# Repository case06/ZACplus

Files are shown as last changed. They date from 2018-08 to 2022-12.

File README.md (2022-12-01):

# ZACplus

[](
    https://opensourceecology.de)

This is the source repo for the ZAC+-Projekt on

https://wiki.opensourceecology.de/Zn/O-Brennstoffzelle

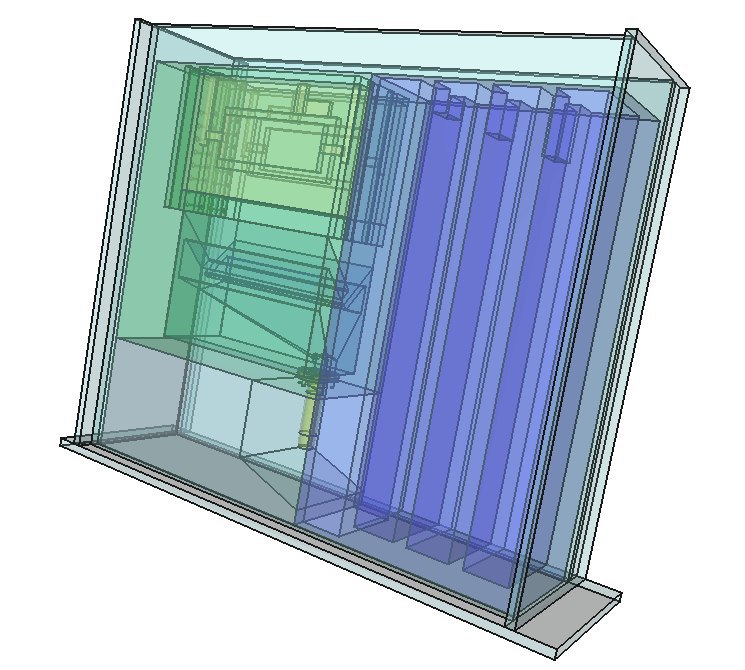
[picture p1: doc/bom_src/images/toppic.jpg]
ZACplus V.1.0
<p>  </p>

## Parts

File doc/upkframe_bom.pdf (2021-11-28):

Seite 1

UPKframe BOM

Partname | UPK-PartNo. | Quantity Description | Supplier

UPKframe
angle2 | 17092223 | 4 | Klemmung f. Tank | ML
angle4 | 17092224 | 2 | Befestigung Mittelquere | ML
angle6 | 17092225 | 8 | Eckverbindung | ML
| | | | ML
flat16 | 17092239 | 3 | f. Interface-mount u. Tank-Kammer-Verbinder | ML
flat24 | 17092240 | 3 | Bodenplatten | ML
| | | | ML
tslot16 | 17092205 | 5 | Mittelquere Front u. Aufrechte | ML
tslot24 | 17092206 | 8 | Rahmen längs u. Aufrechte | ML
tslot40 | 17092208 | 8 | Rahmen längs u. Aufrechte | ML
tslot4con | 17092212 | 2 | Aufdoppelung f. Mittelquere | ML
Tslot16con | 17092216 | 2 | Quere | ML
tslot24con | 17092217 | 8 | Rahmen, quer | ML
| | | | ML
endcap1d | 17092315 | 20 | Endkappen | ML
raconnector | 17092313 | 16 | Eckverbinder | ML
| | | | ML
m6x8 | 17092303 | 64 | Befestigung, 8mm M6, ISO 7380 | ML
m6x12 | 17092304 | 32 | Befestigung, 12mm M6, ISO 7380 | ML
m6x25cyl | 17092307 | 22 | Eckverbindungen, 25mm M6, DIN 7984 | ML
m6nutplate | 17092309 | 64 | Befestigung | ML
m6nut | 17092308 | 4 | Befestigung Interface, M6 DIN 934 | ML
m3x30cyl | 21032809 | 2 | Befestigung Pumpe, 30mm M3, DIN 7984 | ML
m3nut | 19081701 | 6 | Befestigung Pumpe, M§ DIN 934 | ML

Tank
Pumpenplatte_200x160x6 | - | 1 | Montageplatte f. Pumpe, 200x160x6 | 3DP

Seite 2

Supplier | Id | URL
Std.-Part | SP | Standard-Part, widely available from several sources
Makers-Lab ML | http:makers-lab.de
3d-Printable 3DP | 3d-printable part, see project sources
Pumpe | S1 | https://www.ebay.de/itm/351752818084?hash=item51e61a0da4:g:-pYAAOSwEK9TxksN

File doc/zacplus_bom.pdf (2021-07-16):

Seite 1

ZACplus BOM

Partname | PartNo. | Quantity Description | Supplier

Gaskathode
pone7 | 2 | Gaskathodenhalter f. GDL, 3d-part | 3DP
gdlpatch1 | 2 | Gaskathode, Gaskatel MOC | S1
m2kleber | 1 | M2 Neopren Kleber | SP, S2

Zinkanode
oberteil | 1 | Oberteil mit Schlitz f. Zinkplatte | 3DP
seitenteil1b | 2 | zum verbinden mit Oberteil | 3DP
stabilisator1b | 2 | verbindet die Seitenteile unten | 3DP
netz | 1 | muss passend gebogen werden (ev. unter Erwärmung) | 3DP
zinkplatte | 1 | zB. 0,5mm dick, 60x200mm | SP, S3

Cuvette
cuvette_bottom | 1 | Plexiglas 6mm, 412 x 116,4 mm | SP, S4
cuvette_side | 2 | Plexiglas 6mm, 360 x 320 mm | SP, S4
cuvette_frontback | 2 | Plexiglas 6mm, 320 x 116,4 mm | SP, S4
UHUhart | 1 | Kleber f. Plexiglas | SP, S5
silikon | 1 | Eckenfugen ausschmieren | SP, S6

Reaktionskammer
kammer_01 | 1 | Reaktionskammer | 3DP
devolume1 | 1 | Devoluminator | 3DP
emscherbrunnen_01 | 1 | Rutsche/Führung f. Zinc-Slurry | 3DP
schlauchtuelle_03 | 1 | Auslass | 3DP
kaskade1 | 1 | Absetz-Mehrkammersystem | 3DP

Seite 2

Supplier | Id | URL
Std.-Part | SP | Standard-Part, widely available from several sources
Makers-Lab ML | http:makers-lab.de
3d-Printable 3DP | 3d-printable part, see project sources
Gaskatel | S1 | https://gaskatel.de/en/shop/moc-airelectrode-without-ptfe-gasdiffusionlayer/
ebay | S2 | https://www.ebay.de/itm/372711968571?hash=item56c75d4f3b:g:nwYAAOSww6NdKfrM
ebay | S3 | https://www.ebay.de/itm/381164961784?hash=item58bf33bff8:g:qKkAAOSwLs9aYJlP
ebay | S4 | https://www.ebay.de/itm/264805134763?hash=item3da79db1ab:g:sY0AAOSwo8FfGGdu
ebay | S5 | https://www.ebay.de/itm/282102926692?epid=2255354665&hash=item41aea50d64:g:PJwAAOSwiO9Xie7J
ebay | S6 | https://www.ebay.de/itm/124598821921?hash=item1d02ab2421:g:se4AAOSwK-Fgh59I

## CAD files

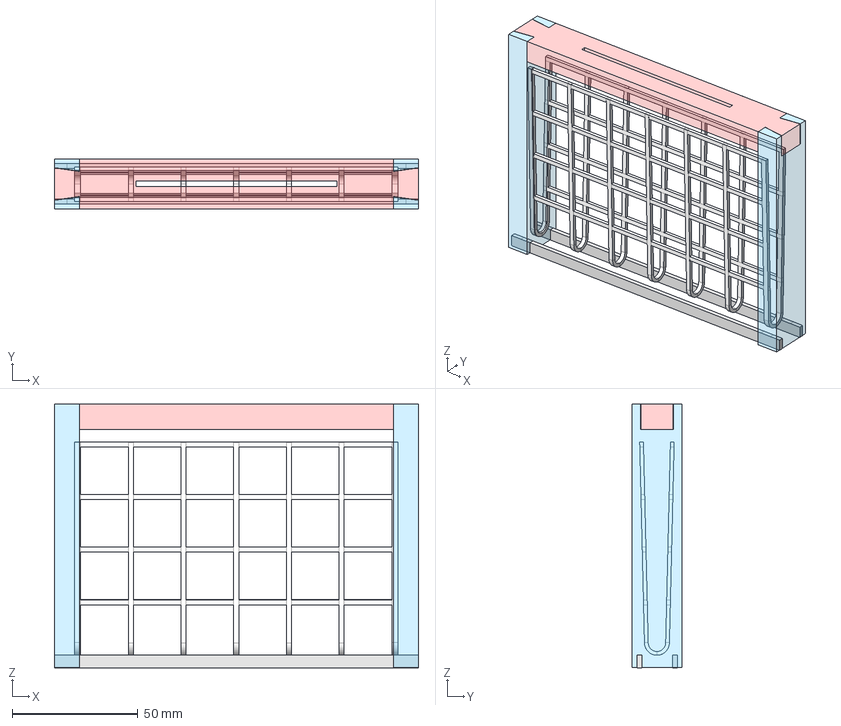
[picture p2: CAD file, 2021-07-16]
cadfiles/zinkanode/Assembly-Zinkplattenhalter.fcstd
145.0 x 19.8 x 105.0 mm
Seitenteil01
Seitenteil01 (Mirror #2)

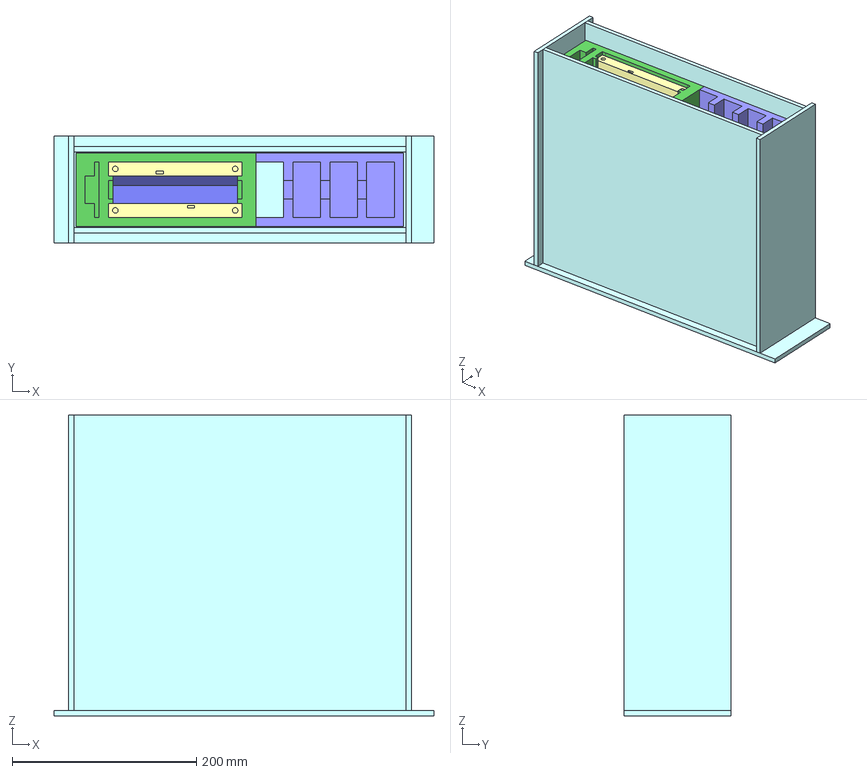
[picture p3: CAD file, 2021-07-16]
cadfiles/kammer/assembly2c.fcstd
412.0 x 116.4 x 326.0 mm
chamber
cascade
devolume
pipe
emscherbrunnen
gdlholder
gdlholder001
cuvette_bottom
cuvette_side
cuvette_side001
cuvette_front
cuvette_front001

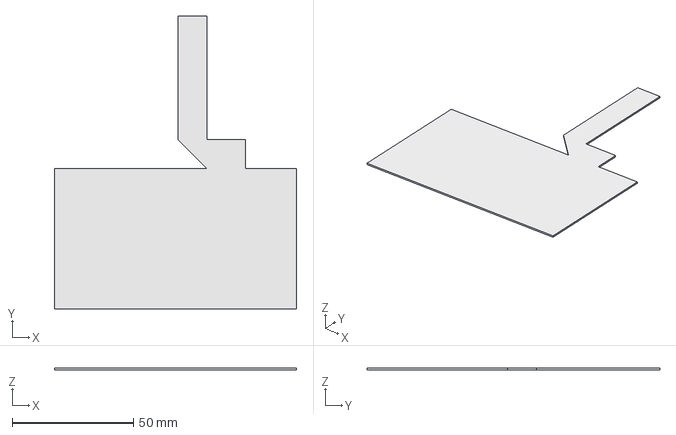
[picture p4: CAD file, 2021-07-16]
cadfiles/gaskathode/gdlpatch1.fcstd
100.0 x 121.0 x 0.7 mm

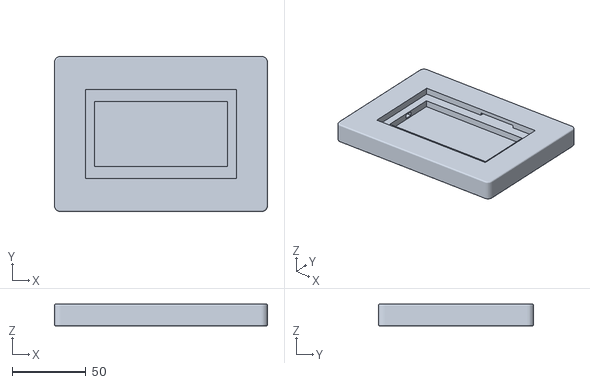
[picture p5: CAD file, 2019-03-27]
cadfiles/gaskathode/stls/pone6b_rounded.stl
144.0 x 105.0 x 14.8

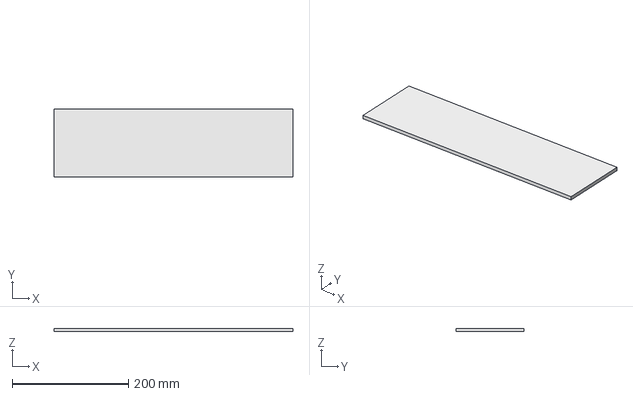
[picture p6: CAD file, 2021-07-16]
cadfiles/kammer/cuvette_bottom.fcstd
412.0 x 116.4 x 6.00 mm

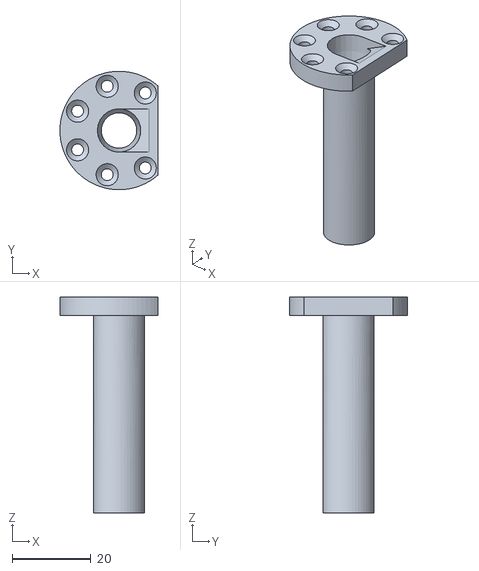
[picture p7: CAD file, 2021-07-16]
cadfiles/kammer/stls/schlauchtuelle_03b.stl
24.9 x 30.0 x 54.8

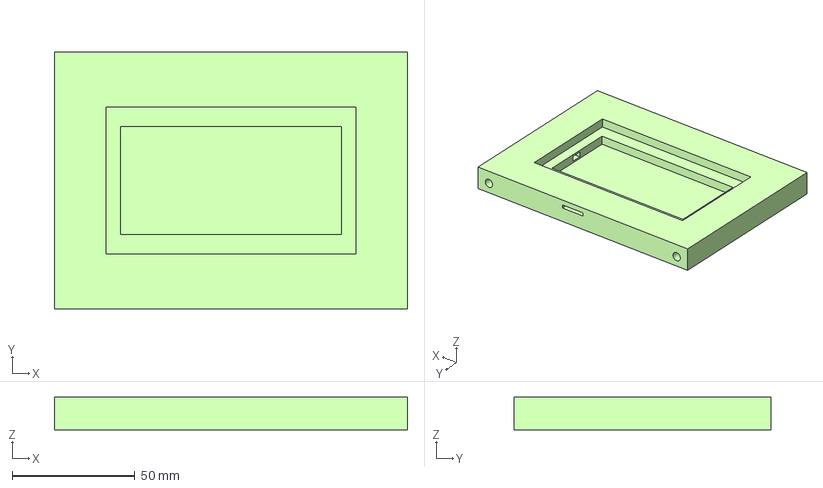
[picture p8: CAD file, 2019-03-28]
cadfiles/gaskathode/pone7.fcstd
144.0 x 105.0 x 13.4 mm

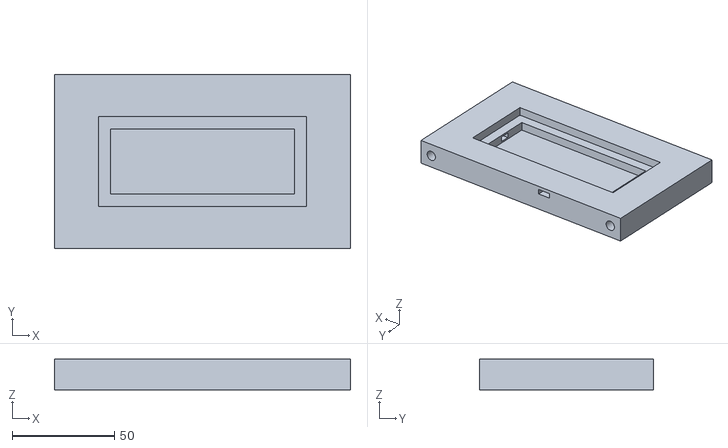
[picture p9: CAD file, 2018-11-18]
cadfiles/gaskathode/stls/pone5.stl
145.0 x 85.0 x 15.0

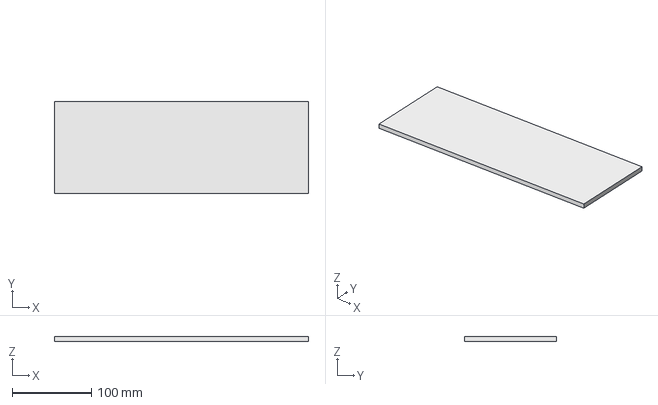
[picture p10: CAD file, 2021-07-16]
cadfiles/kammer/cuvette_frontback.fcstd
320.0 x 116.4 x 6.00 mm

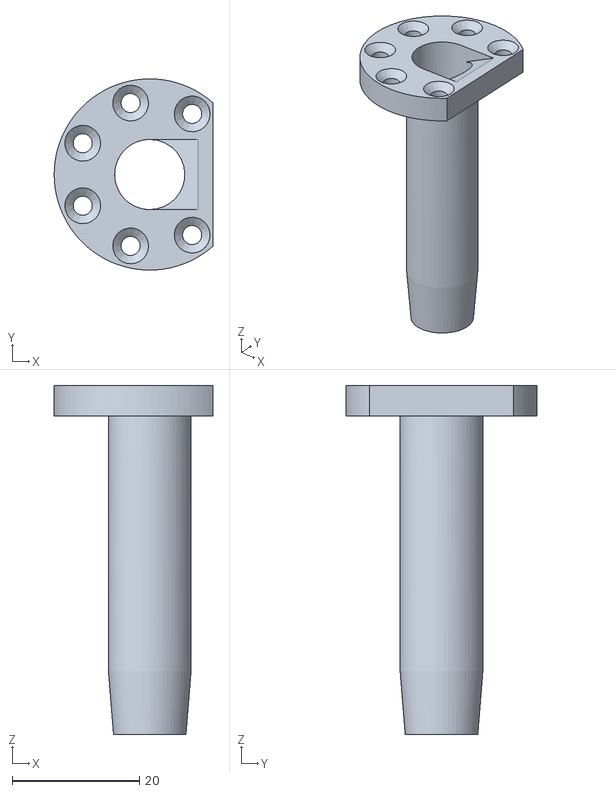
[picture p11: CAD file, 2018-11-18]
cadfiles/kammer/stls/schlauchtuelle_02.stl
24.9 x 30.0 x 54.8

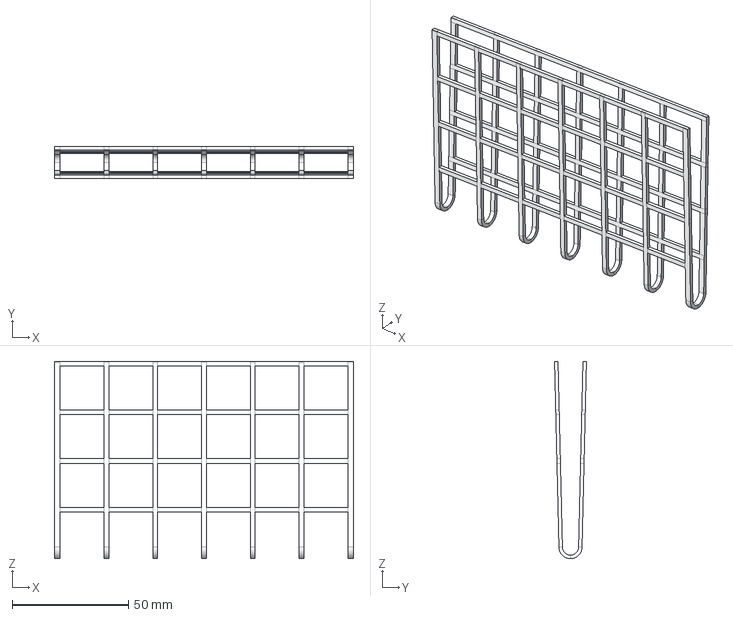
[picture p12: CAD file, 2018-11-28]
cadfiles/zinkanode/Netz_gebogen.fcstd
128.8 x 13.8 x 85.0 mm

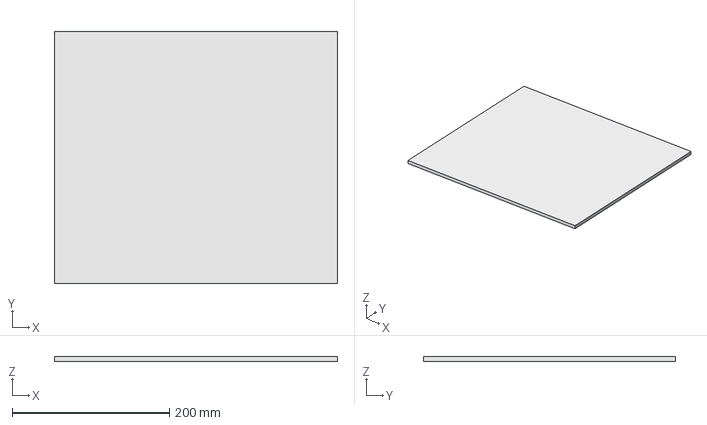
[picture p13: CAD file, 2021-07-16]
cadfiles/kammer/cuvette_side.fcstd
360.0 x 320.0 x 6.00 mm

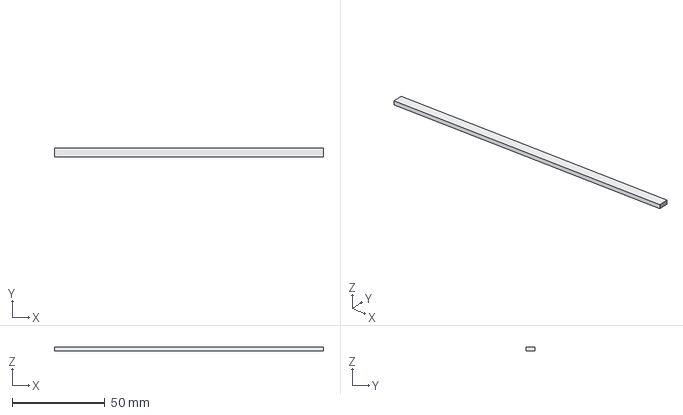
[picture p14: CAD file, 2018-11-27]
cadfiles/zinkanode/Stabilisator1b.fcstd
145.0 x 5.00 x 2.00 mm

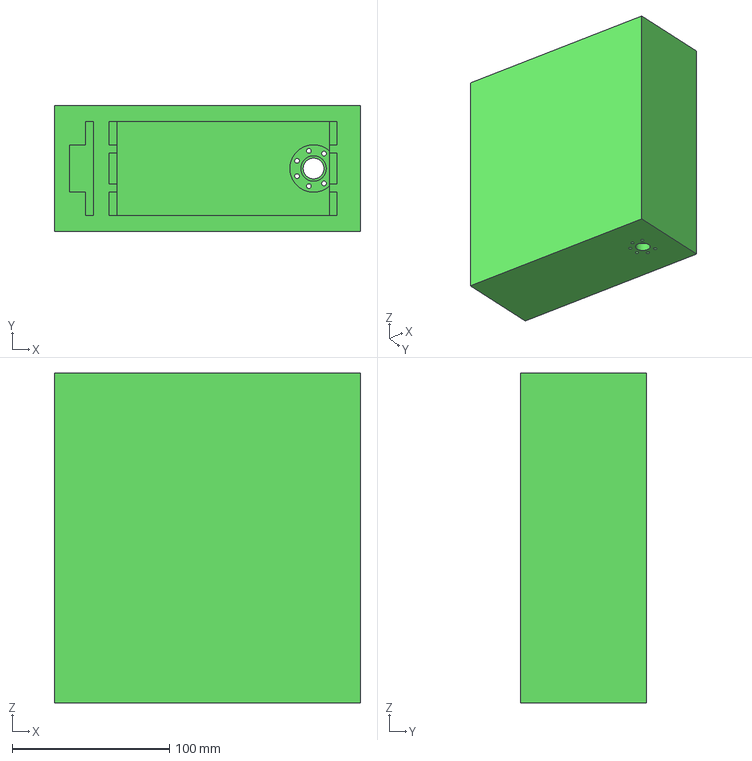
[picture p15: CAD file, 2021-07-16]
cadfiles/kammer/kammer_01.fcstd
195.0 x 80.0 x 210.0 mm

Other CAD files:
cadfiles/gaskathode/pone7_rounded.fcstd
cadfiles/zinkanode/Netz.fcstd
cadfiles/kammer/schlauchtuelle_03.fcstd
cadfiles/zinkanode/Seitenteil1b.fcstd
cadfiles/kammer/devolume1.fcstd
cadfiles/kammer/emscherbrunnen_01.fcstd
cadfiles/kammer/kammer_00.fcstd
cadfiles/kammer/kammer_01_drawdim.fcstd
cadfiles/kammer/kaskade1.fcstd
cadfiles/kammer/stls/devolume1.stl
cadfiles/kammer/stls/emscherbrunnen_01.stl
cadfiles/kammer/stls/kammer_01.stl
cadfiles/kammer/stls/kaskade1.stl
cadfiles/kammer/stls/schlauchtuelle_03.stl
cadfiles/zinkanode/Oberteil.fcstd
cadfiles/zinkanode/stls/netz.stl
cadfiles/zinkanode/stls/oberteil.stl
cadfiles/zinkanode/stls/seitenteil1b.stl
cadfiles/zinkanode/stls/stabilisator1b.stl

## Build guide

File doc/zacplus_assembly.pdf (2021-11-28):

Sheet1

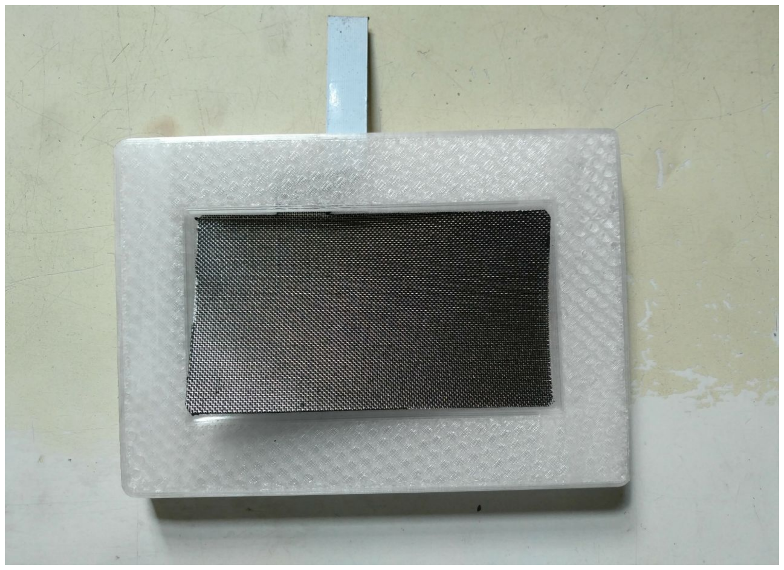
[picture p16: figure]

Page 1

ZACplus Subassemblie BOM

Die Gaskathode mit Halter

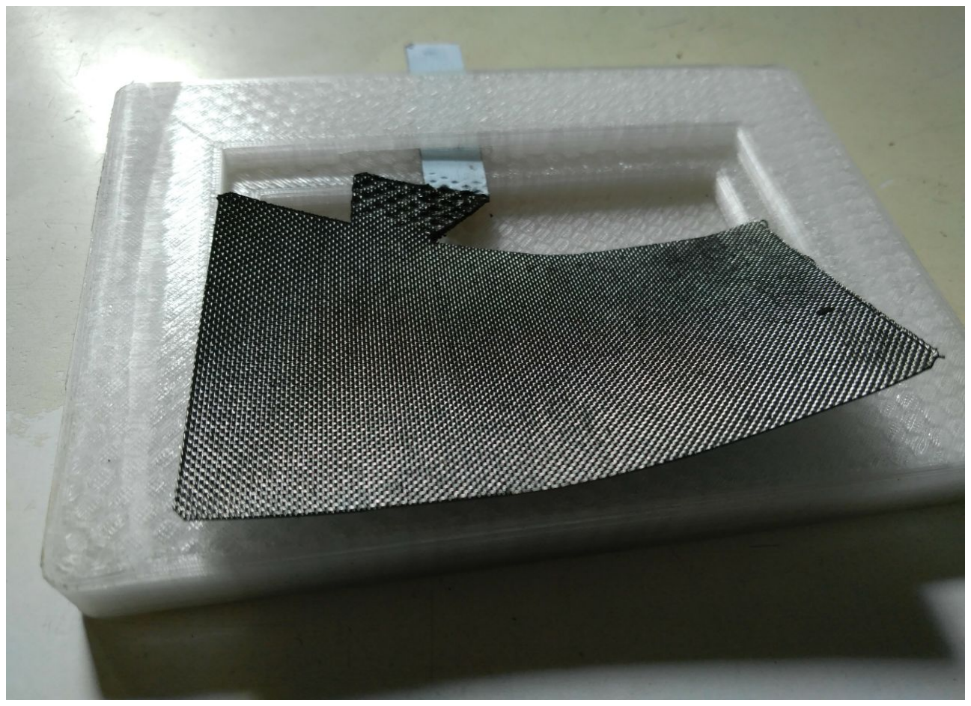
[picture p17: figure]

Sheet1

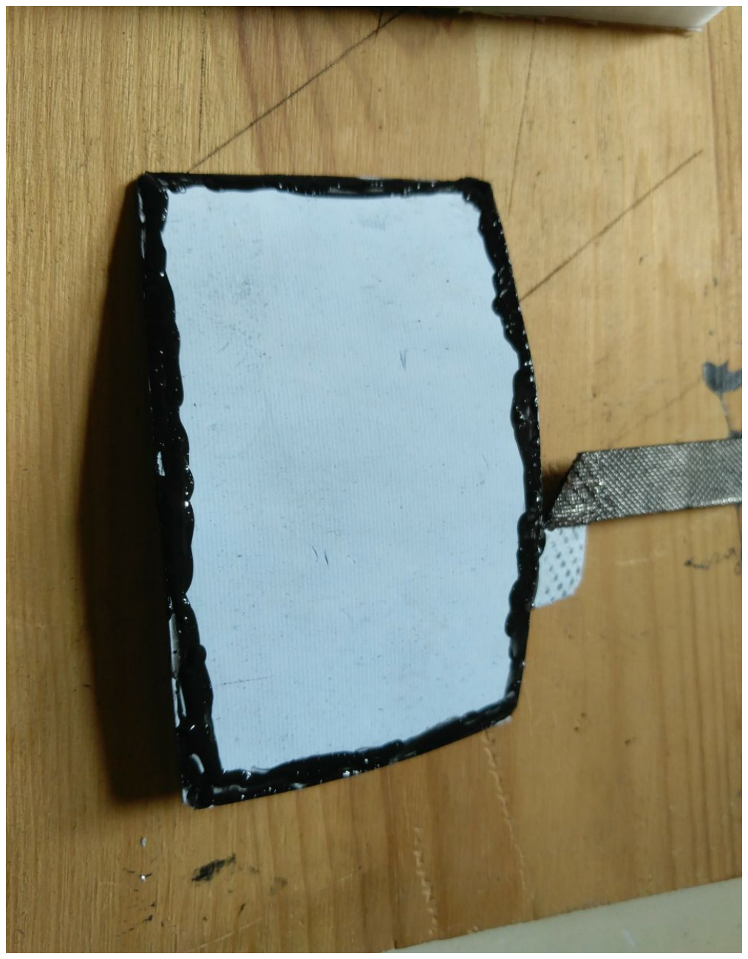
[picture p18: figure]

Page 2

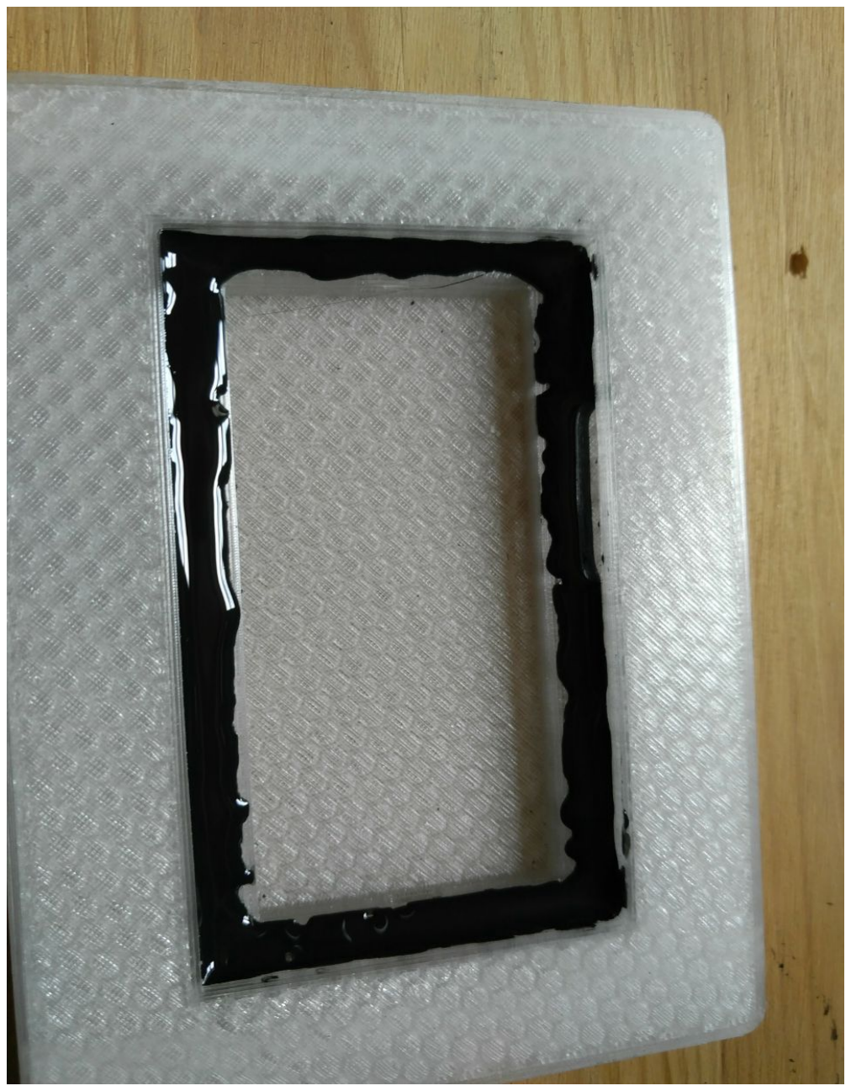
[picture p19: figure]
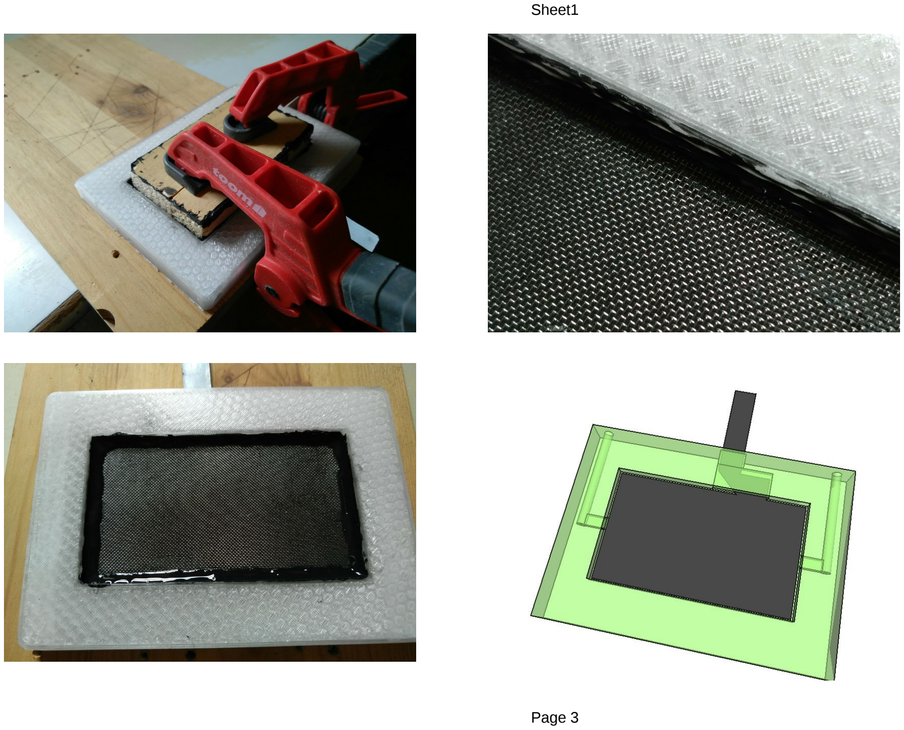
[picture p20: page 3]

Sheet1

Page 3

Sheet1

Page 4

Den GDL-patch passend ausschneiden, die Lasche um 90° drehen/rumbiegen und plattdrücken.

Den Falz vom Gaskathodenhalter mit M2 Kleber bestreichen. Den Rand der GDL auf d. PTFE-Seite ebenfalls mit M2 Kleber versehen. Dann die Lasche der GDL durch den Schlitz im Kathodenhalter fädeln und die GDL mittels Zulage einpressen.

Nun die GDL im Falz nochmal gitterseitig mit M2-Kleber füllen zwecks Abdichtung.

Gaskathode
pone7 | 2 | Gaskathodenhalter f. GDL, 3d-part
gdlpatch1 | 2 | Gaskathode, Gaskatel MOC
m2kleber | 1 | M2 Neopren Kleber

Die Zinkanode mit Halter

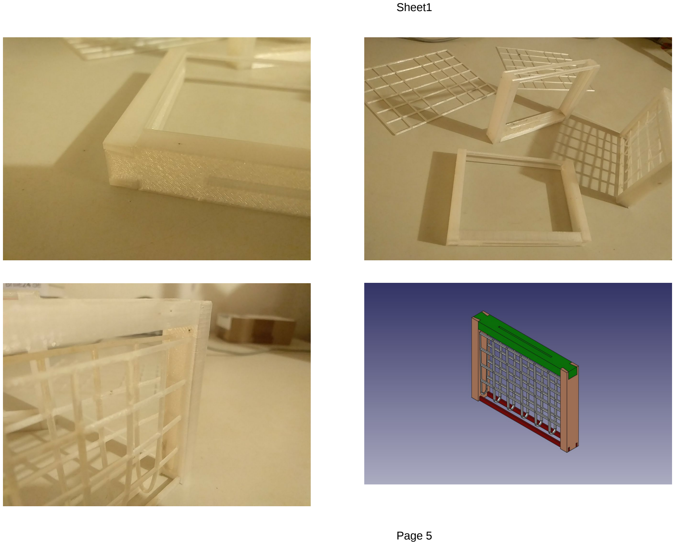
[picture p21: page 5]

Sheet1

Page 5

Sheet1

Page 6

Das Netz passend biegen, dazu den mittleren zu biegenden Bereich leich mit einer Feuerzeugflamme erwärmen.

Das Oberteil und die beiden Seitenteile durch Schwalbenschwanzverbindung verbinden / reindrücken, dazu vorher die Verbindungsstellen mit ABS-Juice (in Azenton gelöstes ABS) bestreichen.

Das gebogene Netz in die Nuten der Seitenteile mit ABS-Juice einkleben.
Die Seitenteile unten mit den STabilisatoren verbinden.

Zinkanode
oberteil | 1 | Oberteil mit Schlitz f. Zinkplatte
seitenteil1b | 2 | zum verbinden mit Oberteil
stabilisator1b | 2 | verbindet die Seitenteile unten
netz | 1 | muss passend gebogen werden (ev. unter Erwärmung)
zinkplatte | 1 | zB. 0,5mm dick, 60x200mm

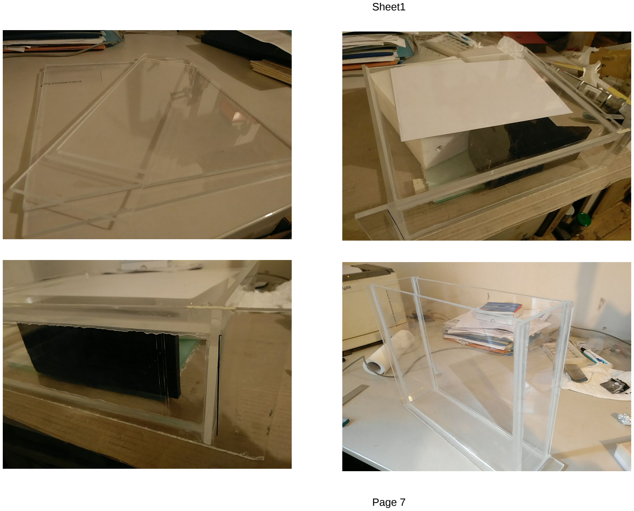
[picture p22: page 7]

Sheet1

Page 7

Die Kammer mit umgebender Cuvette

Sheet1

Page 8

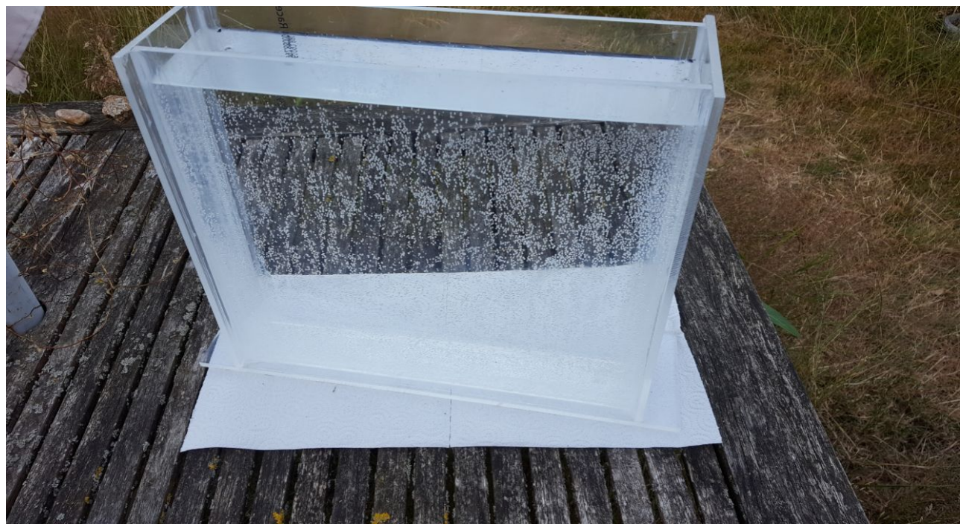
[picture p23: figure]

Den Boden der Cuvette zunächst mit den Seitenteilen verkleben und dann alles mit der einen Seite verkleben. Als Kleber wird UHUhart verwendet.
Dann das Ganze auf die Seite legen, die 3d-gedruckten Kammerteile als Abstandshalter
dazwischenlegen und die noch fehlende Seite aufkleben.
Die Kammerteile müssen leichtgängig einschiebbar sein.
Anschliessend sämtliche Eckfugen mit einer Silikon-Wulst auskleiden zwecks größerer Dichtigkeit. Dichtigkeit abschliessend testen.

Sheet1

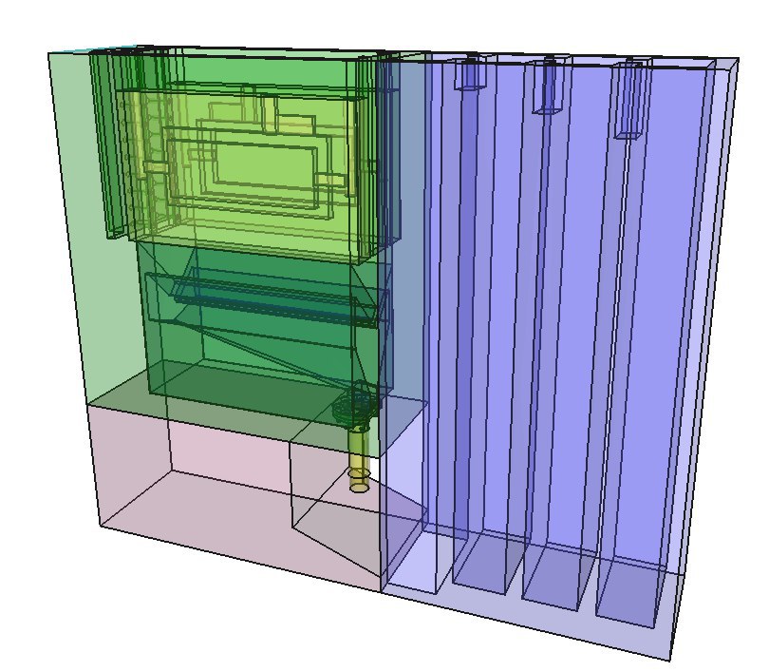
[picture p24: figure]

Page 9

Cuvette
cuvette_bottom | 1 | Plexiglas 6mm, 412 x 116,4 mm
cuvette_side | 2 | Plexiglas 6mm, 360 x 320 mm
cuvette_frontback | 2 | Plexiglas 6mm, 320 x 116,4 mm
UHUhart | 1 | Kleber f. Plexiglas
silikon | 1 | Eckenfugen ausschmieren

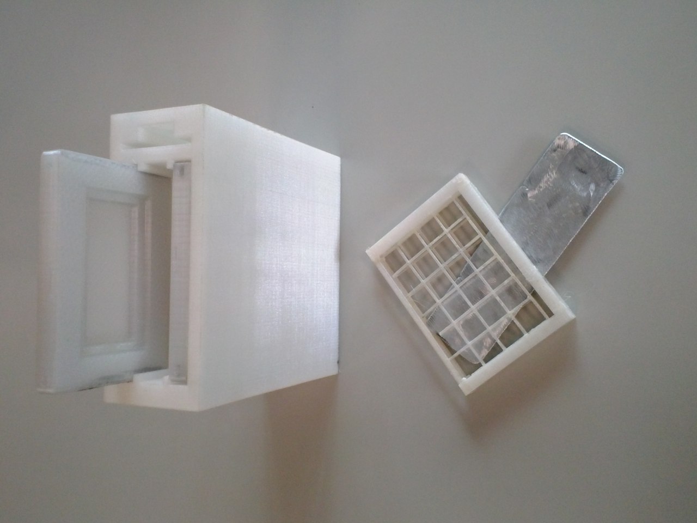
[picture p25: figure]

Sheet1

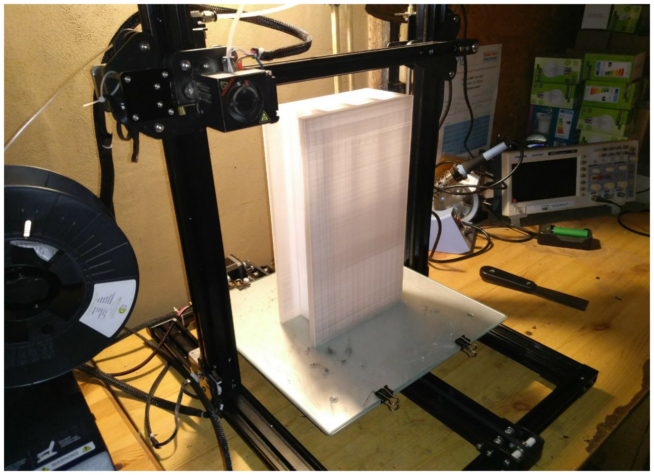
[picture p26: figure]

Page 10

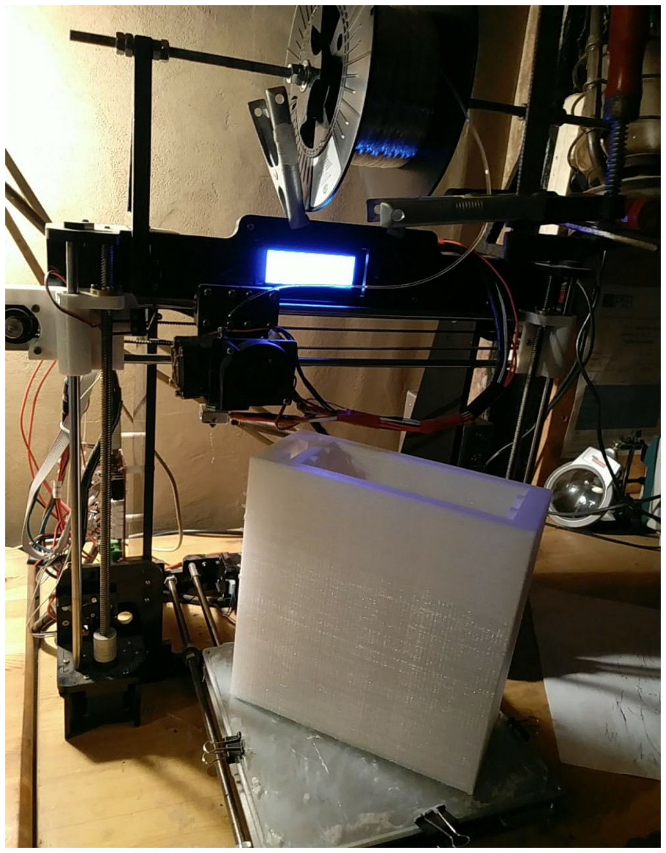
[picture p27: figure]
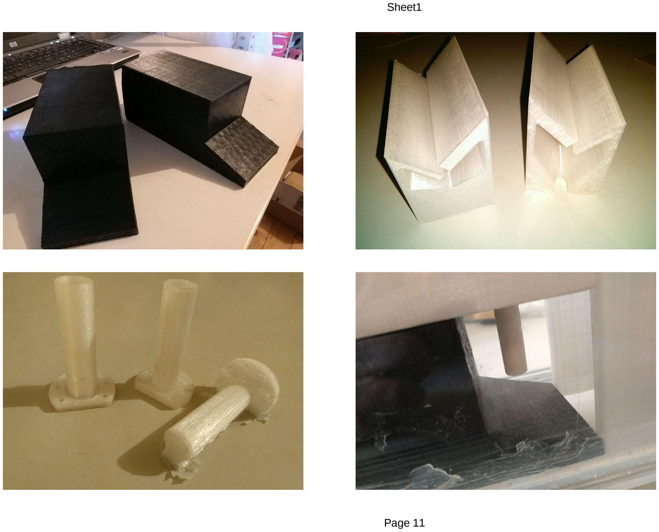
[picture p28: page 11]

Sheet1

Page 11

Sheet1

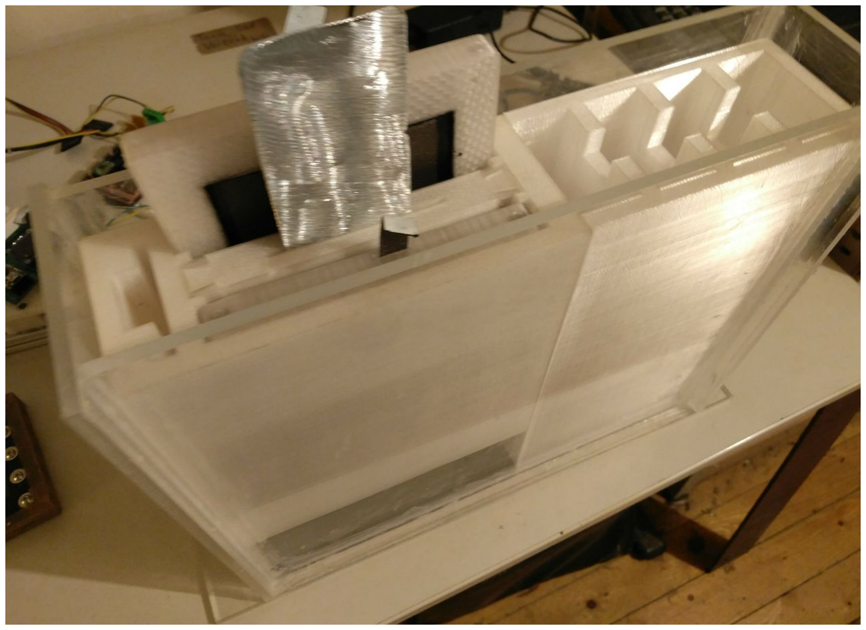
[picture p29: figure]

Page 12

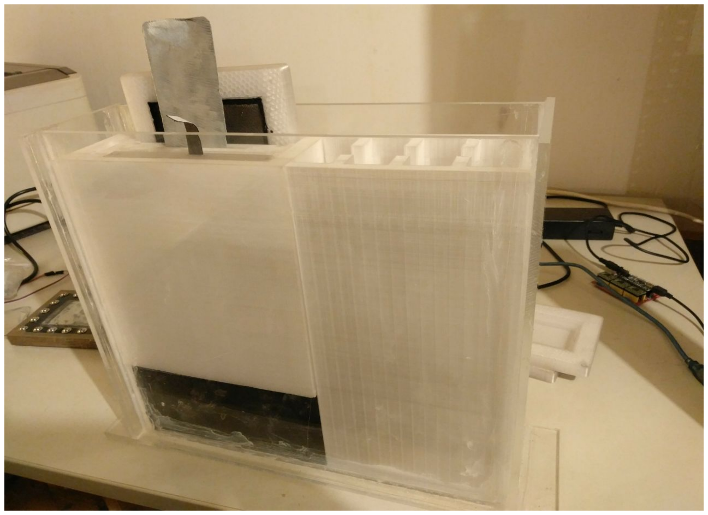
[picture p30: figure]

Die Schlauchtuelle durch die Auslassöffnung am Grunde der Kammer schieben, hält klemmschlüssig.
Dann den Emscherbrunnen in die Kammer schieben. Im oberen Bereich noch die beiden Gaskathodenhalter und den Zinkanodenhalter einschieben.

Nun den Devoluminator in die Cuvette schieben und die Kammer oben drauf setzen. Den verbleibenden Raum
daneben in der Cuvette mit der Kaskadenkammer ausfüllen, indem das Kaskaden-Modul dort eingeschoben wird.

Reaktionskammer
kammer_01 | 1 | Reaktionskammer
devolume1 | 1 | Devoluminator
emscherbrunnen_01 | 1 | Rutsche/Führung f. Zinc-Slurry
schlauchtuelle_03 | 1 | Auslass
kaskade1 | 1 | Absetz-Mehrkammersystem

Sheet1

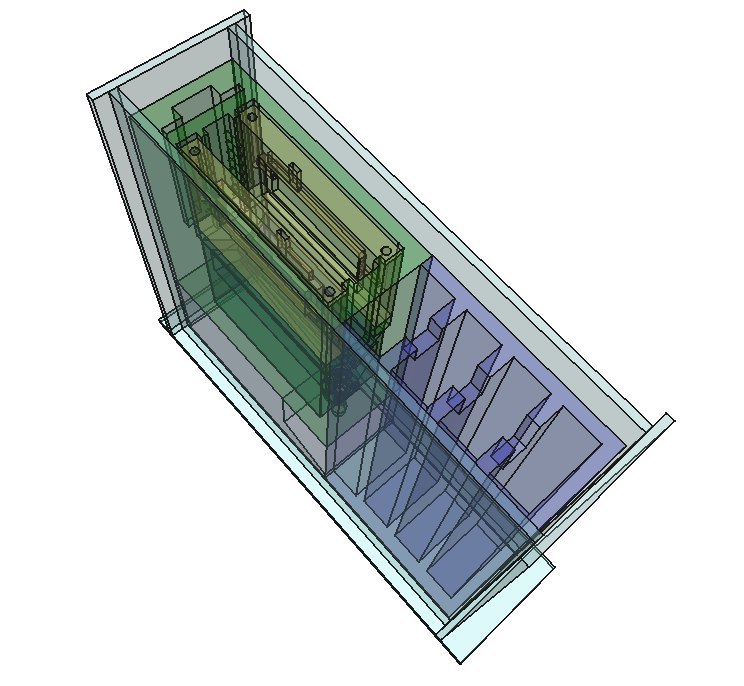
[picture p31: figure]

Page 13


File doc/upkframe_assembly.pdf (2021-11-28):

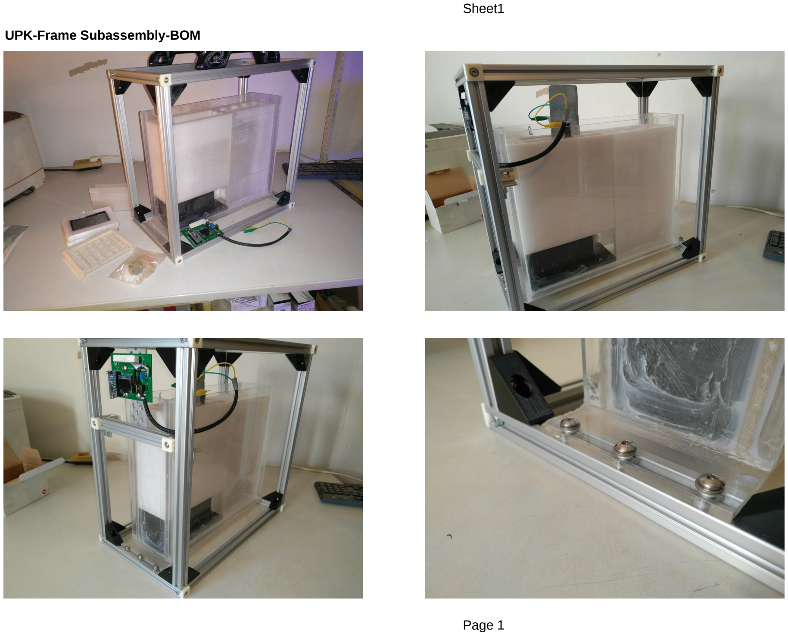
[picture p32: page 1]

Sheet1

Page 1

UPK-Frame Subassembly-BOM

Sheet1

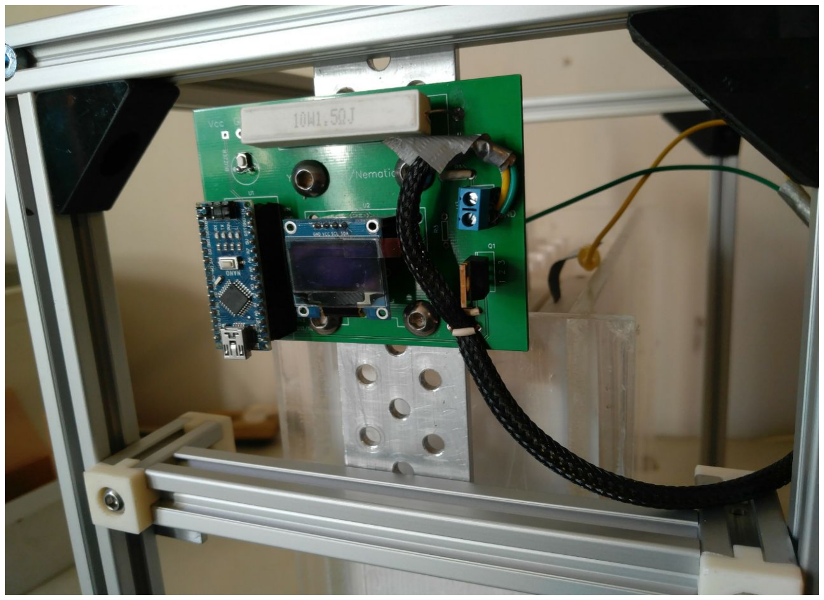
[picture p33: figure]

Page 2

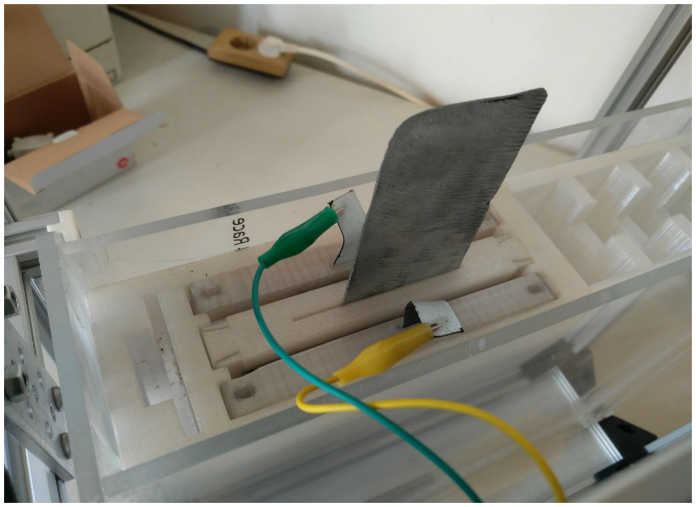
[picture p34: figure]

Unterer u. oberer Rahmen f. Kammer
tslot24con | 4 | Rahmen, quer
tslot40 | 4 | Rahmen längs
m6x25cyl | 8 | Eckverbindungen
endcap1d | 8 | Endkappen
m6x8 | 8 | Befestigung Endkappen

Sheet1

Page 3

Aufrechte f. Rahmen
tslot40 | 4 | Rahmen Aufrechte
raconnector | 16 | Eckverbinder
m6x12 | 16 | Befestigung Eckverbinder
m6nutplate | 16 | Befestigung Eckverbinder

Mittelquere
tslot16 | 1 | Mittelquere Front
tslot4con | 2 | Aufdoppelung f. Mittelquere
m6x25cyl | 2 | Eckverbindung Mittelquere
endcap1d | 4 | Endkappen
m6x8 | 4 | Befestigung Endkappen
angle4 | 2 | Befestigung Mittelquere
m6nutplate | 4 | Befestigung Mittelquere
m6x8 | 4 | Befestigung Mittelquere

Interface-Träger
flat16 | 1 | f. Interface-Montage
m6nutplate | 4 | Befestigung flat16
m6x8 | 4 | Befestigung flat16
m6x12 | 4 | Befestigung Interface
m6nut | 4 | Befestigung Interface

Verbindung Kammer-Tank
flat16 | 2 | Verbindet Tankmodul mit Kammer
m6nutplate | 8 | Befestigung flat16
m6x8 | 8 | Befestigung flat16

Sheet1

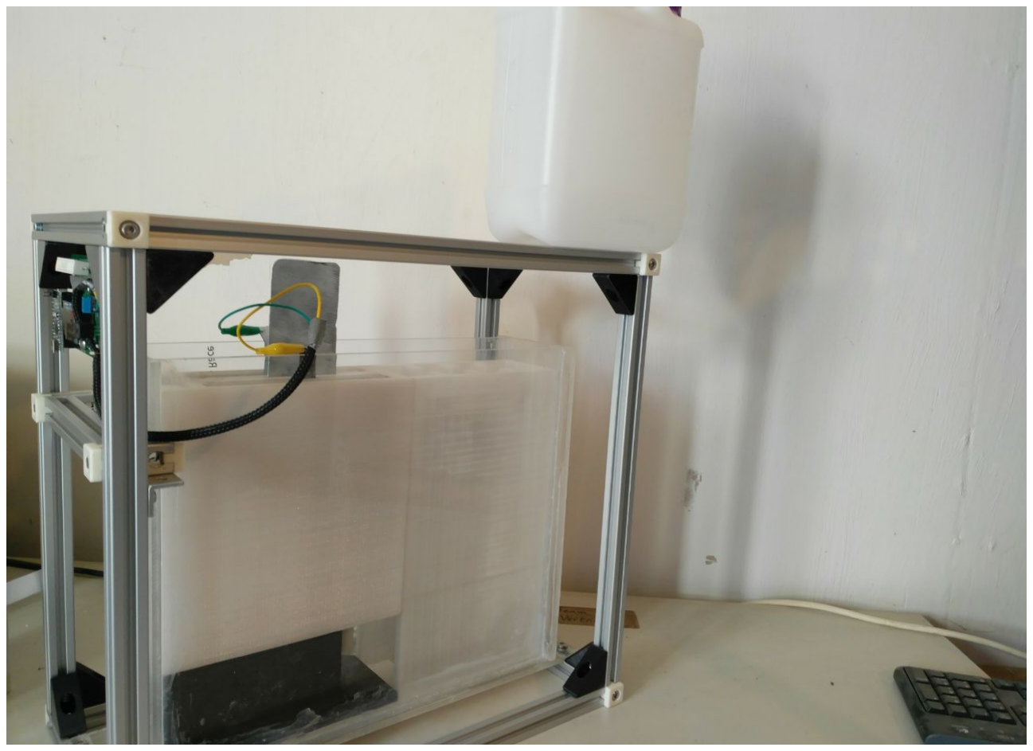
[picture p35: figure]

Page 4

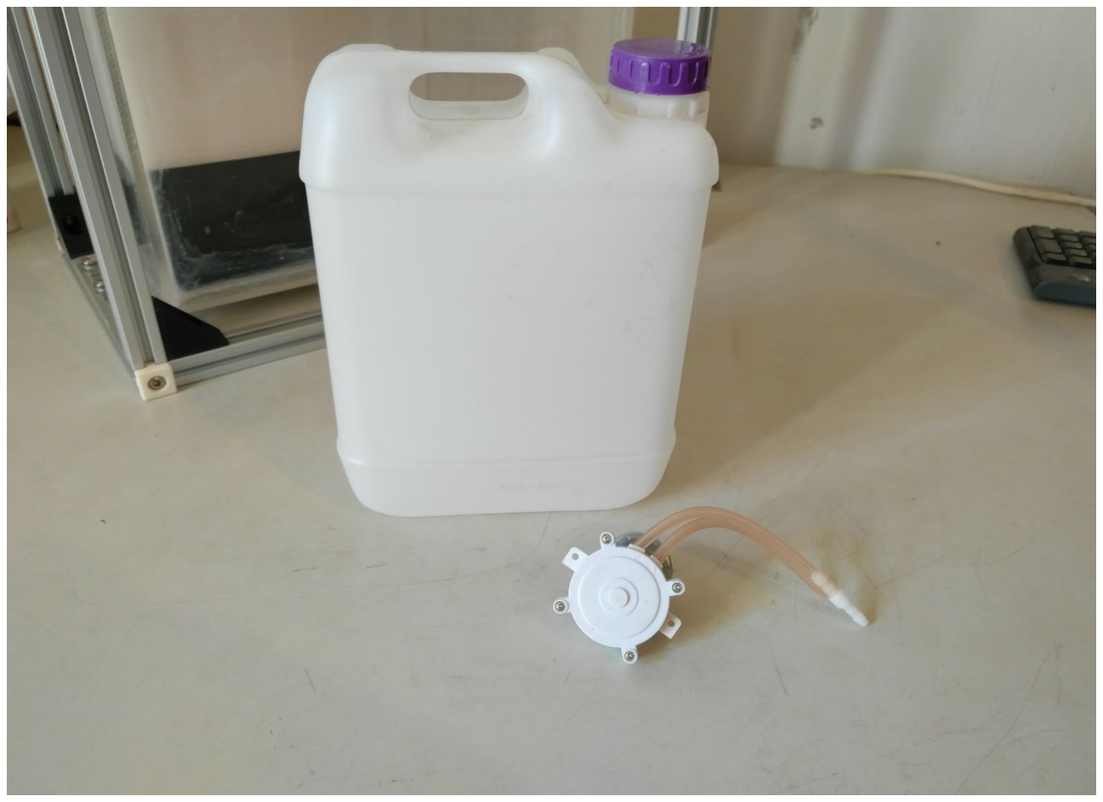
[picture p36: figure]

Sheet1

Page 5

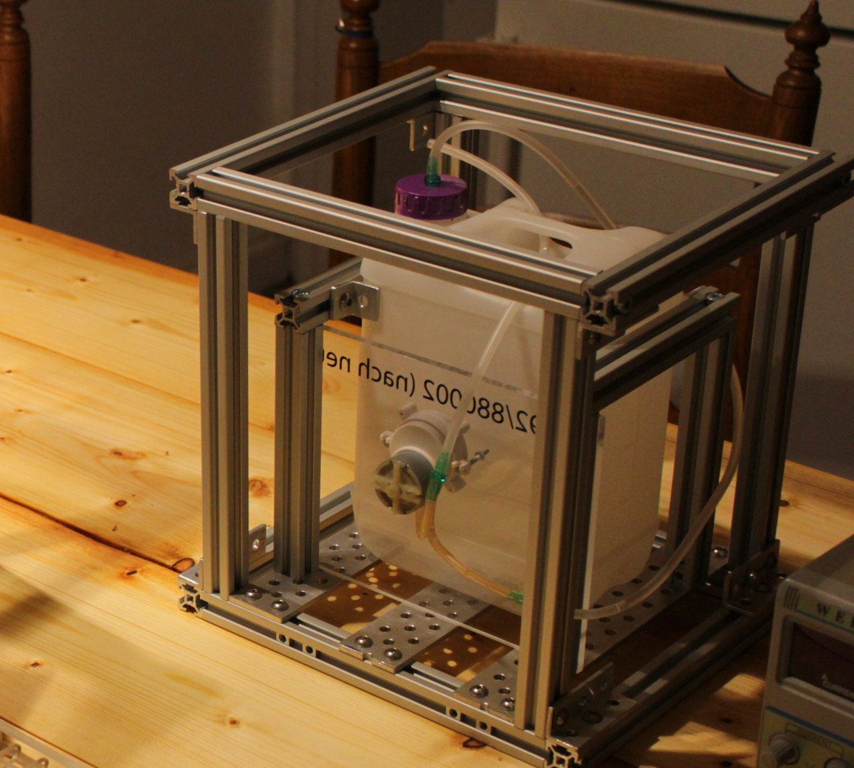
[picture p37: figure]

Unterer u. oberer Rahmen f. Tank
tslot24con | 4 | Rahmen, quer
tslot24 | 4 | Rahmen längs
m6x25cyl | 8 | Eckverbindungen
endcap1d | 8 | Endkappen
m6x8 | 8 | Befestigung Endkappen

Aufrechte f. Rahmen
tslot24 | 4 | Rahmen Aufrechte

Sheet1

Page 6

angle6 | 8 | Eckverbindung
m6nutplate | 16 | Befestigung Eckverbindung
m6x8 | 16 | Befestigung Eckverbindung
flat24 | 3 | Bodenplatten
m6nutplate | 12 | Befestigung Bodenplatten
m6x8 | 12 | Befestigung Bodenplatten

Tankhalter
Tslot16con | 2 | Quere
Tslot16 | 4 | Aufrechte
m6x25cyl | 4 | Befestigung oben
m6x12 | 4 | Befestigung unten
angle2 | 4 | Klemmung f. Tank
m6x12 | 4 | Befestigung angle2

Zirkulationspumpe
Pumpenplatte_200x160 | 1 | Montageplatte f. Pumpe
m6x12 | 4 | Befestigung d. Platte
m6nutplate | 4 | Befestigung d. Platte
circulationpump12v24l | 1 | Peristaltikpumpe, 24L/h
m3x30 | 2 | Befestigung Pumpe
m3nut | 6 | Befestigung Pumpe

Tank
Tank2.5L | 1 | 2,5L-Behälter, 220x160x100
Schlauch6mm | 2 | Silikonschlauch 6mm, 50mm
Stutzen 6mm | 3 | Anschlussstutzen f. Schlauch

Sheet1

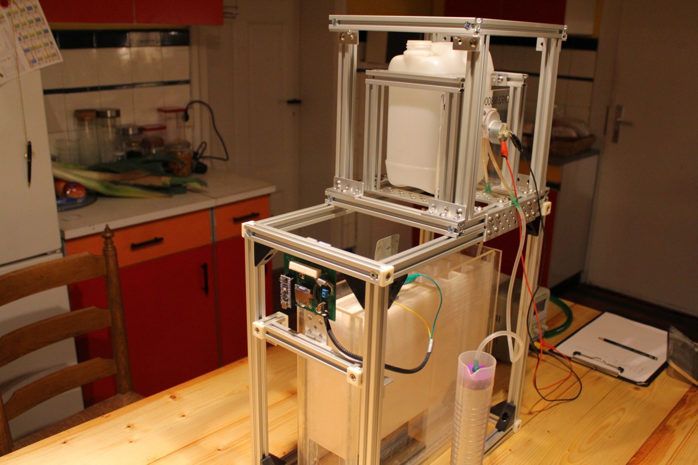
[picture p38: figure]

Page 7

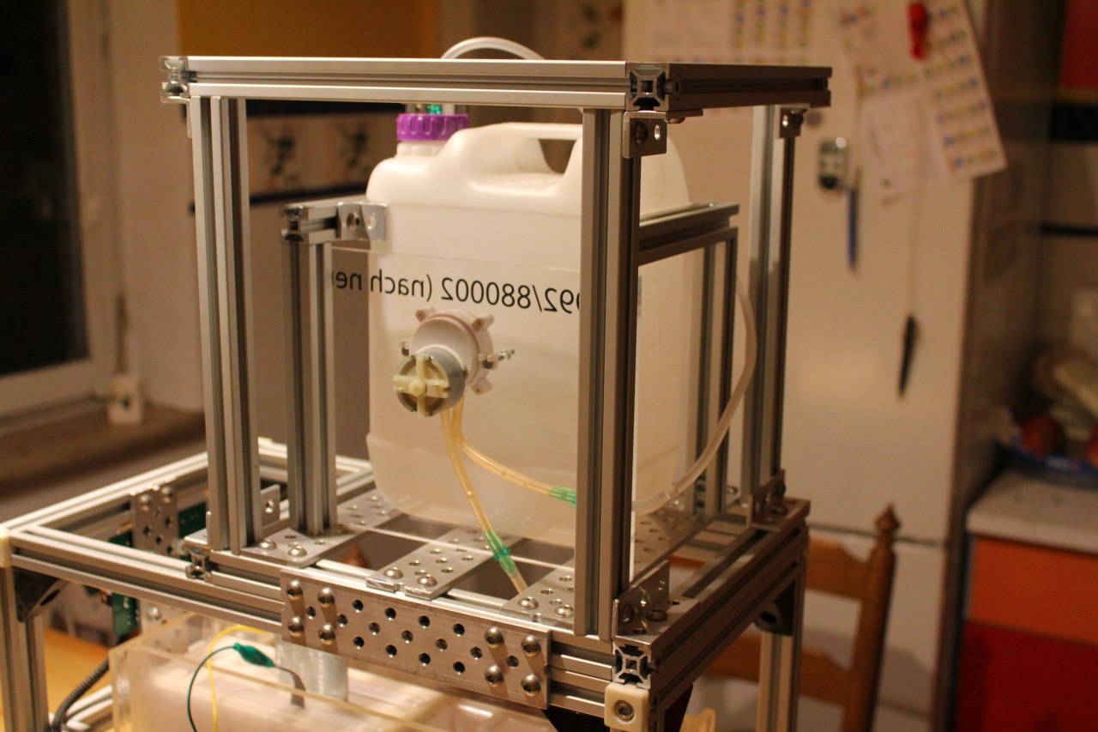
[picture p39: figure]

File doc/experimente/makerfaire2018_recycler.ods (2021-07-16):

mA | V
0 | 1,7
10 | 1,8
20 | 1,9
40 | 2
80 | 2,1
110 | 2,2
130 | 2,3
170 | 2,4
210 | 2,5
230 | 2,6
290 | 2,7
340 | 2,8
380 | 2,9
420 | 3
470 | 3,1
490 | 3,2
530 | 3,3
560 | 3,4
600 | 3,5
640 | 3,6
670 | 3,7
700 | 3,8
740 | 3,9
770 | 4
810 | 4,1
850 | 4,2
900 | 4,3
940 | 4,4
970 | 4,5
1020 | 4,6
1050 | 4,7
1080 | 4,8
1100 | 4,9
1160 | 5
1200 | 5,1
1240 | 5,2
1280 | 5,3
1300 | 5,4
1320 | 5,5
1360 | 5,6
1410 | 5,7
1450 | 5,8
1500 | 5,9
1520 | 6
1600 | 6,1
1650 | 6,2
1670 | 6,3
1680 | 6,4

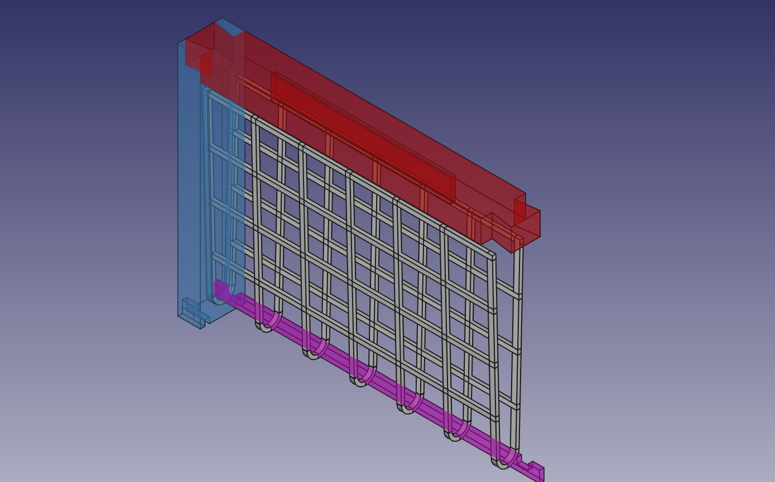
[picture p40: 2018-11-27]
cadfiles/zinkanode/images/anodenhalter_assembly5.png

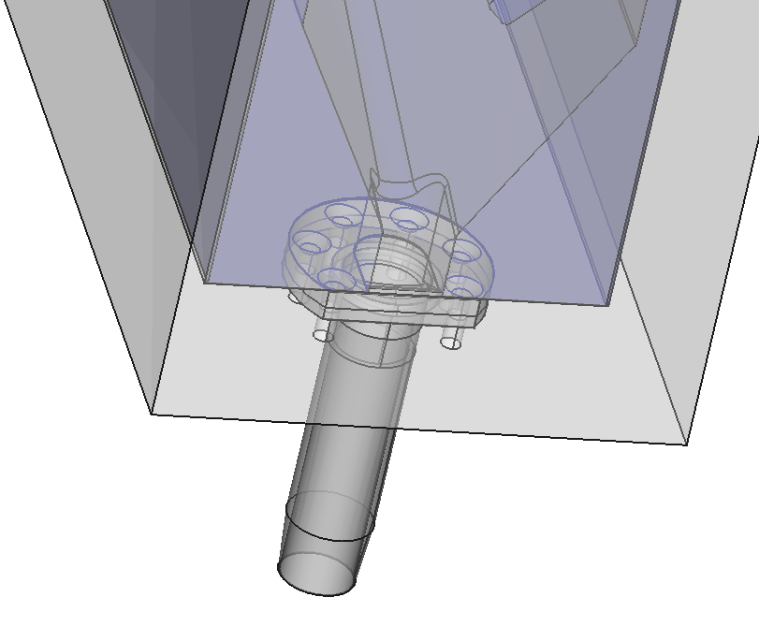
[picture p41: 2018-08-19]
cadfiles/kammer/images/assembly_01.png

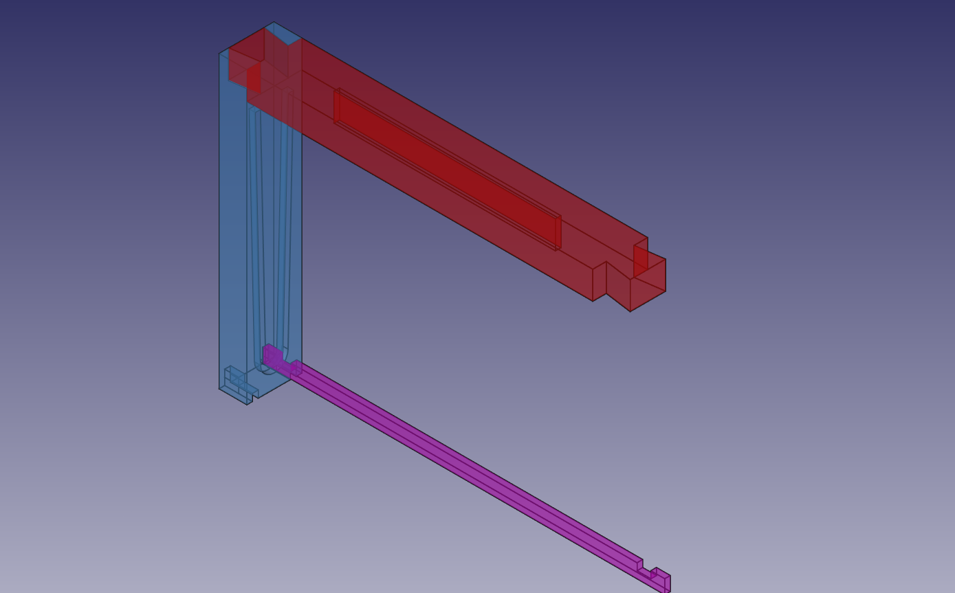
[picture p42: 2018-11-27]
cadfiles/zinkanode/images/anodenhalter_assembly4.png

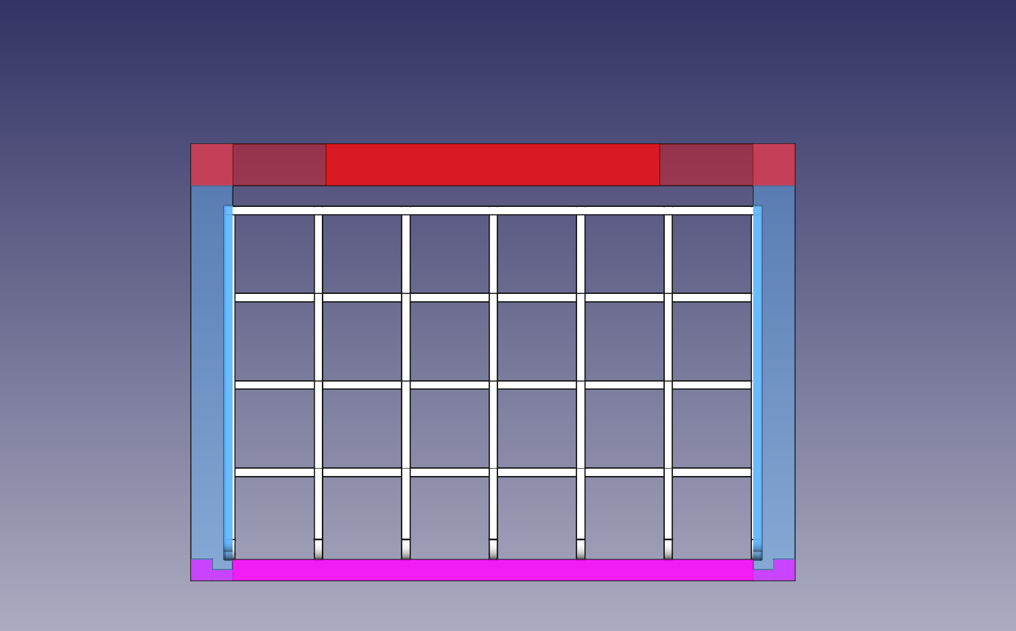
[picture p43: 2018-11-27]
cadfiles/zinkanode/images/anodenhalter_assembly6_seite.png

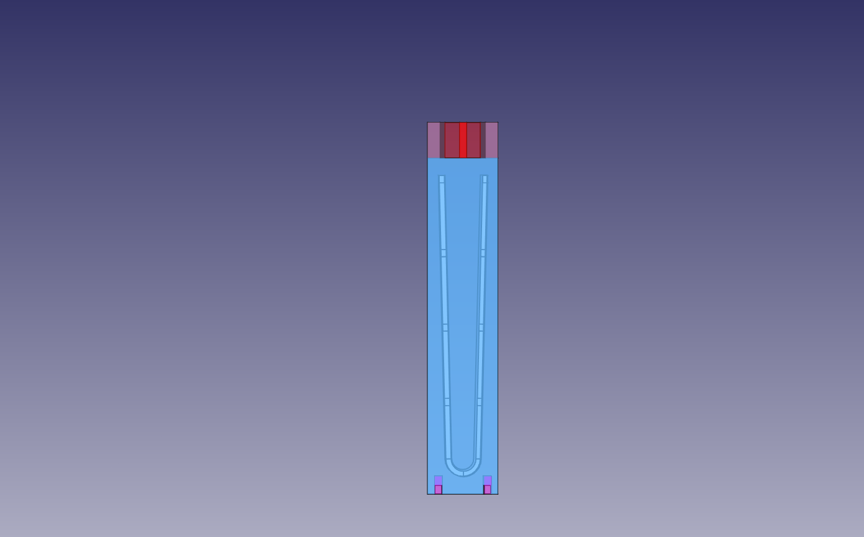
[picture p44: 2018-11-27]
cadfiles/zinkanode/images/anodenhalter_assembly6_seite_vorne.png

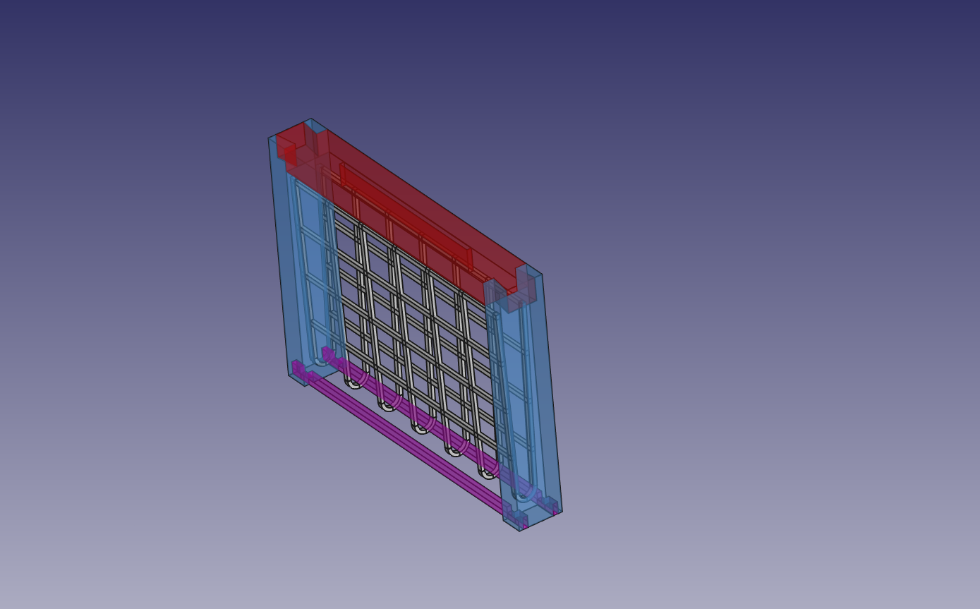
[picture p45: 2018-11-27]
cadfiles/zinkanode/images/anodenhalte_assembly1.png

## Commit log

2018-08-19 added letest Freecad files
    [assembly_01.fcstd, emscherbrunnen_01.fcstd, kammer_01.fcstd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]
2018-09-26 added pre-version of chamber
    [kammer_00.fcstd]
2018-10-09 added devolume,cascade, tube and assembly files
    [assembly1b.fcstd, devolume1.fcstd, kaskade1.fcstd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]
2018-11-14 added folder for .stl-files
    [emscherbrunnen_01.stl, kammer_01.stl]
2018-11-18 added some .stl-files
    [devolume1.stl, kaskade1.stl, schlauchtuelle_02.stl]
2018-11-27 added Zinkanodenhalter
    [Netz.fcstd, Oberteil.fcstd, Seitenteil.fcstd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]
2018-11-28 added assembly-pic
2018-11-28 added assembly files
    [Assembly-Zinkplattenhalter.fcstd, Netz_gebogen.fcstd]
2019-03-27 reworked dimensions an rounded edges
    [gdlpatch1.fcstd, pone6.fcstd, pone6b.fcstd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]
2019-03-27 removed pone6c.fcstd
    [pone6c.fcstd]
2019-03-28 added 3d-print-optimized version
    [pone7.fcstd, pone7_rounded.fcstd]
2020-03-15 README: mini generalization (in case we move the repo elsewhere)
2021-07-16 minor changes
    [Assembly-Zinkplattenhalter.fcstd, Seitenteil.fcstd, Stabilisator.fcstd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]
2021-07-16 some minor structural changes
    [Assembly-Zinkplattenhalter.fcstd, Netz.fcstd, Netz_gebogen.fcstd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]
2021-07-16 changed filename
    [upkframe_assembly.ods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]
2021-07-16 changed docs
    [upkframe_assembly.ods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]
2021-11-28 formatted guide
    [upkframe_assembly.ods]
2022-12-01 added oseg custombadge
    [upkframe_bom.ods]
